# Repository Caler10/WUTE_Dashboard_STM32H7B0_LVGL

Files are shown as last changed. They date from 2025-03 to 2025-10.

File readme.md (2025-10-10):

# 针对WUTE车队电动方程式赛车开发的多功能仪表 WUTE_Dashboard

本人负责设计开发的WUTE第一代多功能自制仪表（该项目也是2023自创项目“针对电动方程式赛车开发的车身电子监控与人机交互系统”的人机交互部分），该仪表基于STM32H7B0VET6，采用5寸TFT高亮屏(800nit)，使用LVGL图形库绘制GUI界面并实时刷新赛车监测数据，具体功能如下：

功能说明：
1. 实时采集整车跑动数据，并在屏幕上实时刷新显示
2. 具备屏幕亮度随环境光自动调节功能
3. 集成跑马灯功能
4. 支持与整车CAN通讯
5. 集成2.4G无线数传模块（ESP8266模块）
6. 集成激活按钮、待驶按钮以及TSOFF、BMS、IMD指示灯

# 设计说明

## 硬件说明

硬件设计方面，采用立创EDA开发，四层板设计

PCB设计展示：

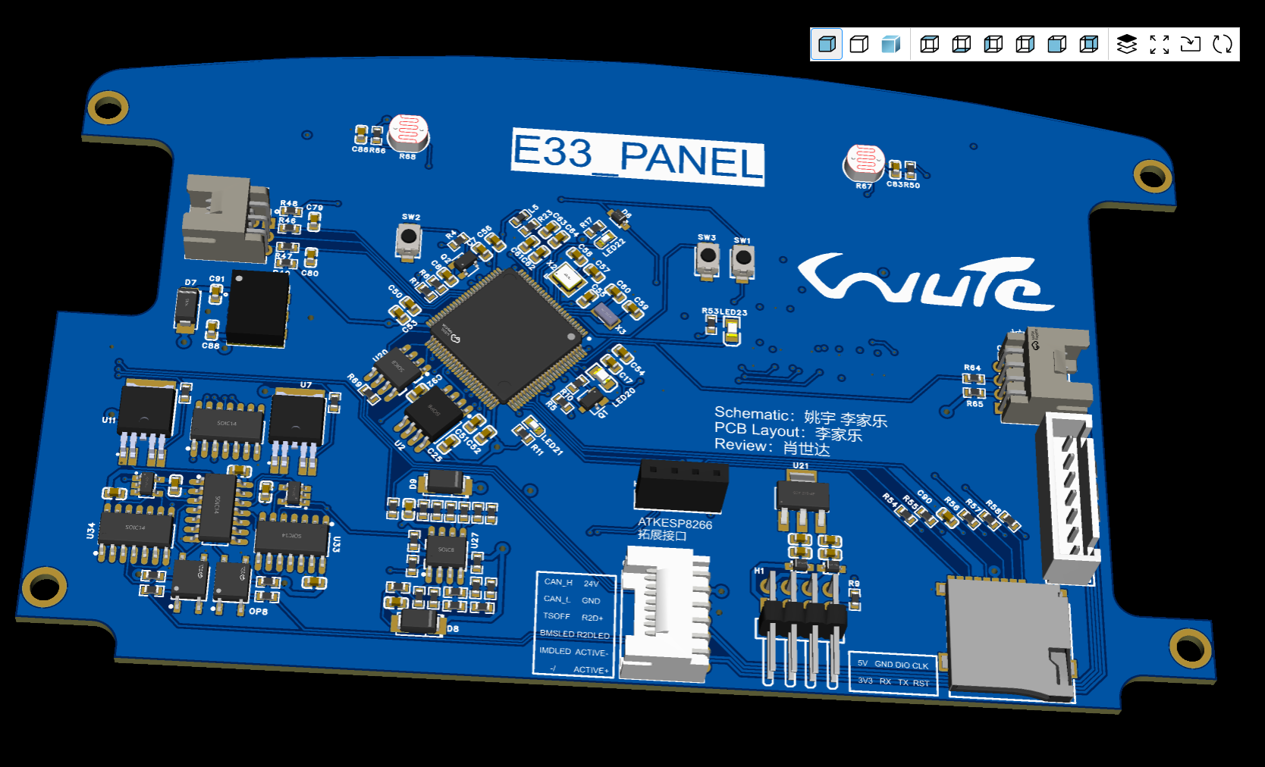
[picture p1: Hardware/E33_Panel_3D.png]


## 软件说明

开发平台：STM32H7B0VET6

开发环境：STM32cubeMX+Keil+VSCode

WUTE_Dashboard嵌入式软件分为Bootloader+App（为实现外部flash加载），App软件基于前后台的裸机系统开发，GUI采用LVGL图形库开发

App软件架构：基于CORE层+BSP层（+中间层LVGL）+APP层的架构开发

项目代码展示：

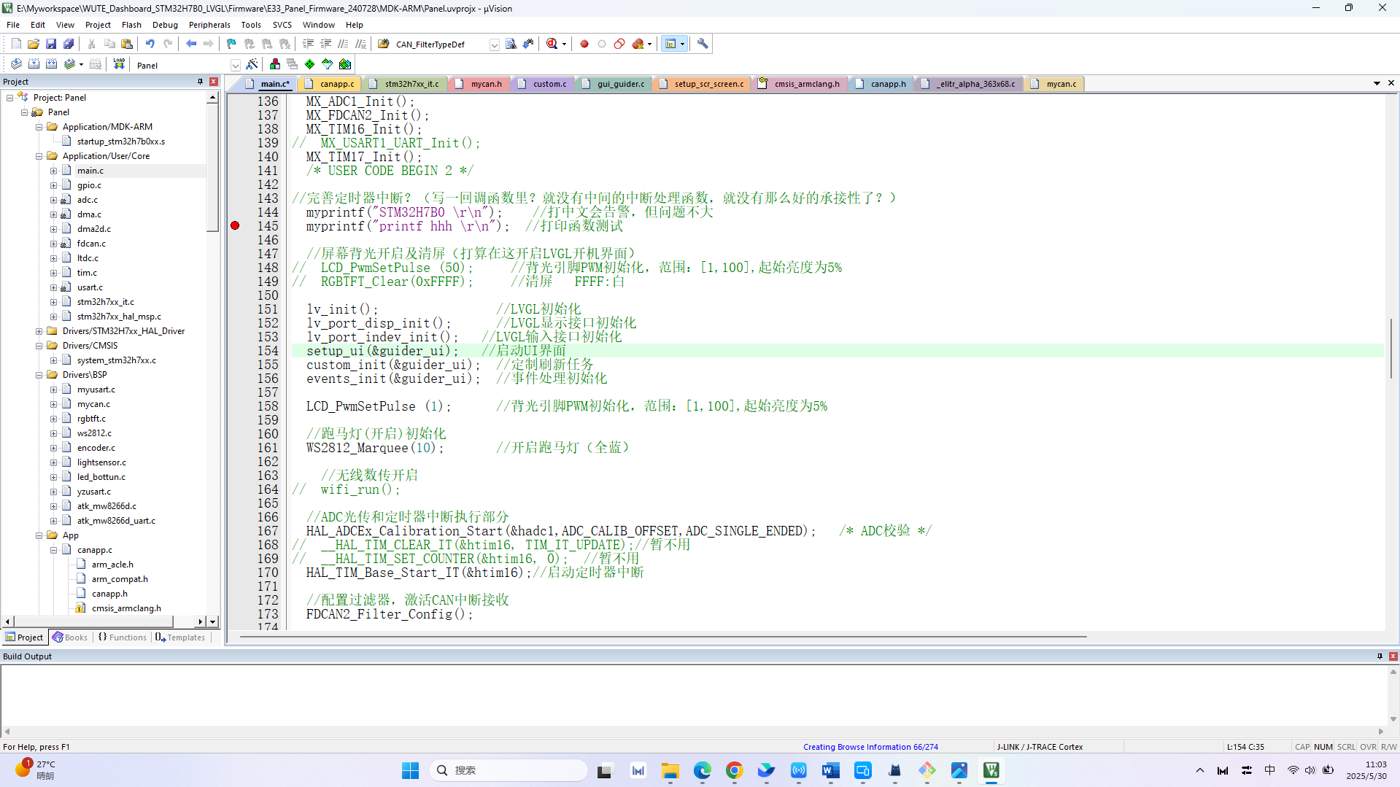
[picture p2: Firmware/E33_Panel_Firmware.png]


## 模型设计

仪表外壳分为前板和后板，仪表驱动板和屏幕封装在模型内部，通过沉头螺栓和热熔螺母进行固定，前后板之间采用密封胶填充间隙

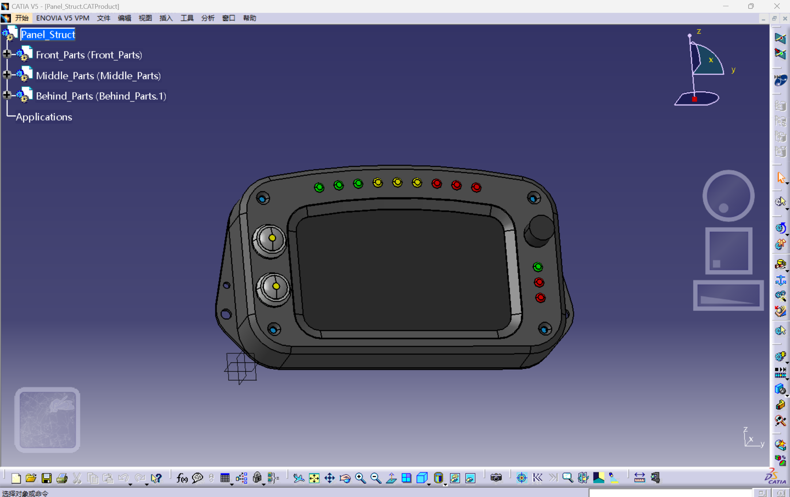
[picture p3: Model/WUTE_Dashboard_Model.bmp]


## GUI设计

仪表板界面UI采用单界面设计，在单界面整合了包括高压电池（电压、电流、温度、电量）、电机控制器（温度）、电机（转速、温度、功率）、各车身设备工作状态、DRS和TCS开启状态，以及制动油压、加速开度、转矩千分比等信息

GUI设计界面：

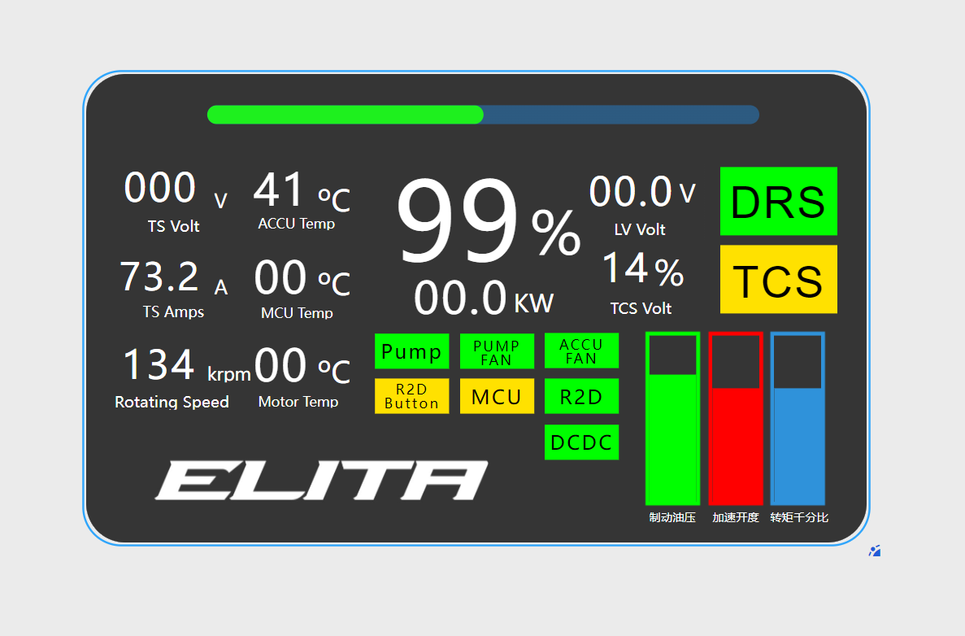
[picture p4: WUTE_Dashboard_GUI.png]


# 测试

屏幕静态显示测试，屏幕可正常显示设计的UI界面：

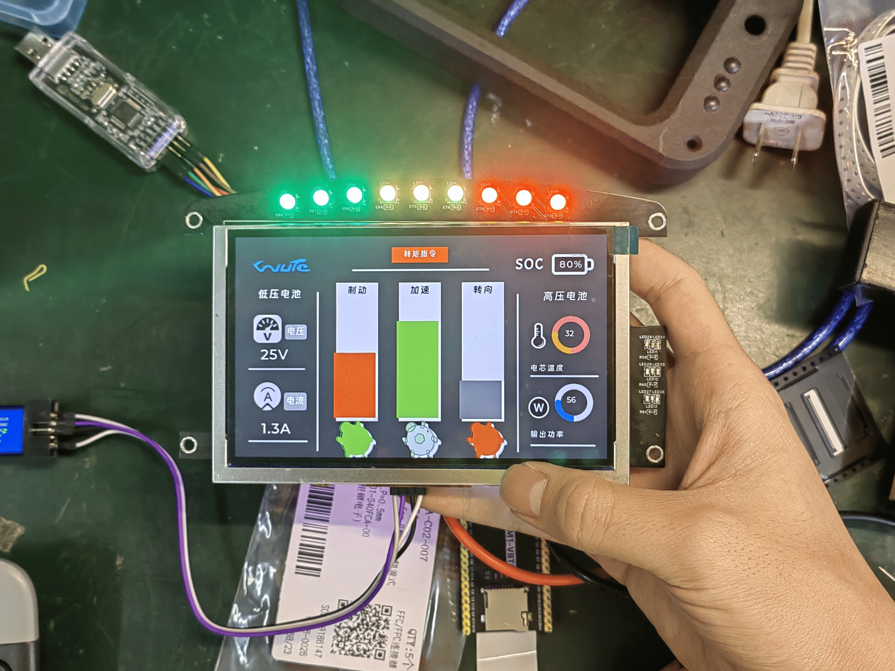
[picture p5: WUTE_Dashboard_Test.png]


屏幕动态刷新测试，仪表可正常解析CAN总线报文并将相关信息实时在屏幕和跑马灯上刷新：



# 项目成果

该仪表已顺利搭载在了WUTE车队2023赛季E33赛车和2024赛季E10赛车上并持续稳定运行，成为了赛车状况监测与可视化的重要途径，同时验证了其具备良好的抗振性与防水性

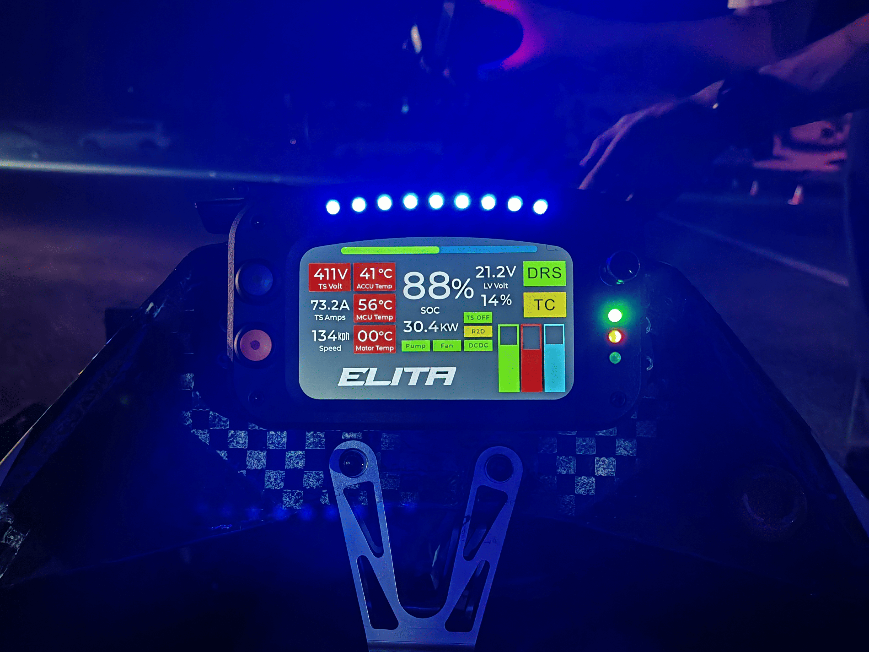
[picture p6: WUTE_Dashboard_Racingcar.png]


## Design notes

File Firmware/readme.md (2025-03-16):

# E33_Panel/WUTE_Dashboard裸机程序

开发平台：STM32H7B0VBT6
开发环境：MX+keil+VScode

---

# 软件架构

HAL库       
BSP         board support pack
APP         功能实现层
main函数    负责总调用执行

---

# 注意事项

无线透传的引脚未上位
慎用printf，加了相关的头文件，不报错但是会进半主机（导致不进main函数）然后无论烧录还是调试都执行不了程序找不到原因

开启了TIM7的定时器中断，现在主程序运行不了，中断程序也运行不了，除非把TIM中断关掉，就算在定时器中断不写任何东西，也还是这个问题
具体：运行不主动进主程序，进调试能使运行完主程序，然后进调试RESET后有报错Cannot access Memory (@ 0xe00ffff0, Read, Acc Size: 4 Byte)
2024.1.30回顾：是进半主机的问题

---

# 待完善问题

小心中断回调抢占导致低优先级的中断执行不了

跑马灯：
清屏＋跑马灯第一个灯灭不了

光传
已改，测试正常工作

串口打印
方案一：用自己的打印函数（只可打印），
方案二：使用MicroLIB来实现，哪种方案更好待考究
方案三：借鉴原子的透传打印函数（可打印可接收）

无线数传
wifi_run()；初始化正常，是ESP8266没有应答
原因：供电流不足

# 开发日志

## 20240411

最初可用版本

## 20240726

接入PDB、VCU报文
优化GUI显示
拓展PUMP、DRS、R2D按钮、MCU Ready、低压电池电压等数据的显示
调整跑马灯驱动（由随电池箱输出功率改为随电机转速变化），降低跑马灯亮度
解决DRS按钮按下DRS启动延时大的问题，仪表、VCU共用对PDB的指令报文
对照DBC校核显示数据（无误）

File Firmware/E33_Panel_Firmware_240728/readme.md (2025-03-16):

/**
 **********************************************************************************************************
 *项目名称：E33_Panel_裸机版程序
 *开发平台：STM32H7B0VBT6
 *开发环境：MX+keil+VScode
 **********************************************************************************************************
 */

/**********************************************************************************************************/
现况：
开启了TIM7的定时器中断，现在主程序运行不了，中断程序也运行不了，除非把TIM中断关掉，就算在定时器中断不写任何东西，也还是这个问题
具体：运行不主动进主程序，进调试能使运行完主程序，然后进调试RESET后有报错Cannot access Memory (@ 0xe00ffff0, Read, Acc Size: 4 Byte)
2024.1.30回顾：是进半主机的问题

/**********************************************************************************************************/

软件架构：
HAL库
BSP（board support pack）
APP
main总调用执行

/**********************************************************************************************************/

注意事项：
无线透传的引脚未上位
慎用printf，加了相关的头文件，不报错但是会进半主机（导致不进main函数）然后无论烧录还是调试都执行不了程序找不到原因

/**********************************************************************************************************/

待改进：小心中断回调抢占导致低优先级的中断执行不了

跑马灯：
清屏＋跑马灯第一个灯灭不了

光传
已改，测试正常工作

串口打印
方案一：用自己的打印函数（只可打印），
方案二：使用MicroLIB来实现，哪种方案更好待考究
方案三：借鉴原子的透传打印函数（可打印可接收）

无线数传
wifi_run()；初始化正常，是ESP8266没有应答
原因：供电流不足

20240726更新日志：
接入PDB、VCU报文
优化GUI显示
拓展PUMP、DRS、R2D按钮、MCU Ready、低压电池电压等数据的显示
调整跑马灯驱动（由随电池箱输出功率改为随电机转速变化），降低跑马灯亮度
解决DRS按钮按下DRS启动延时大的问题，仪表、VCU共用对PDB的指令报文
对照DBC校核显示数据（无误）

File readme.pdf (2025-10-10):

readme.md | 2025-10-10

# 针对WUTE车队电动方程式赛车开发的多功能仪表

# WUTE_Dashboard

本人负责设计开发的WUTE第一代自制仪表（该项目也是2023自创项目“针对电动方程式赛车开发的车身电子监 控与人机交互系统”的人机交互部分），一款基于STM32H7B0VET6，采用5寸TFT高亮屏(800nit)，使用LVGL图形 库绘制GUI界面并实时刷新赛车监测数据的多功能仪表，具体功能如下：

功能说明：

1. 集成跑马灯功能
2. 实时采集整车跑动数据，并在屏幕上实时刷新显示
3. 具备屏幕亮度随环境光自动调节功能
4. 支持与整车CAN通讯
5. 集成2.4G无线数传模块（ESP8266模块）
6. 集成激活按钮、待驶按钮以及TSOFF、BMS、IMD指示灯

# 设计说明

## 硬件说明

PCB设计展示：

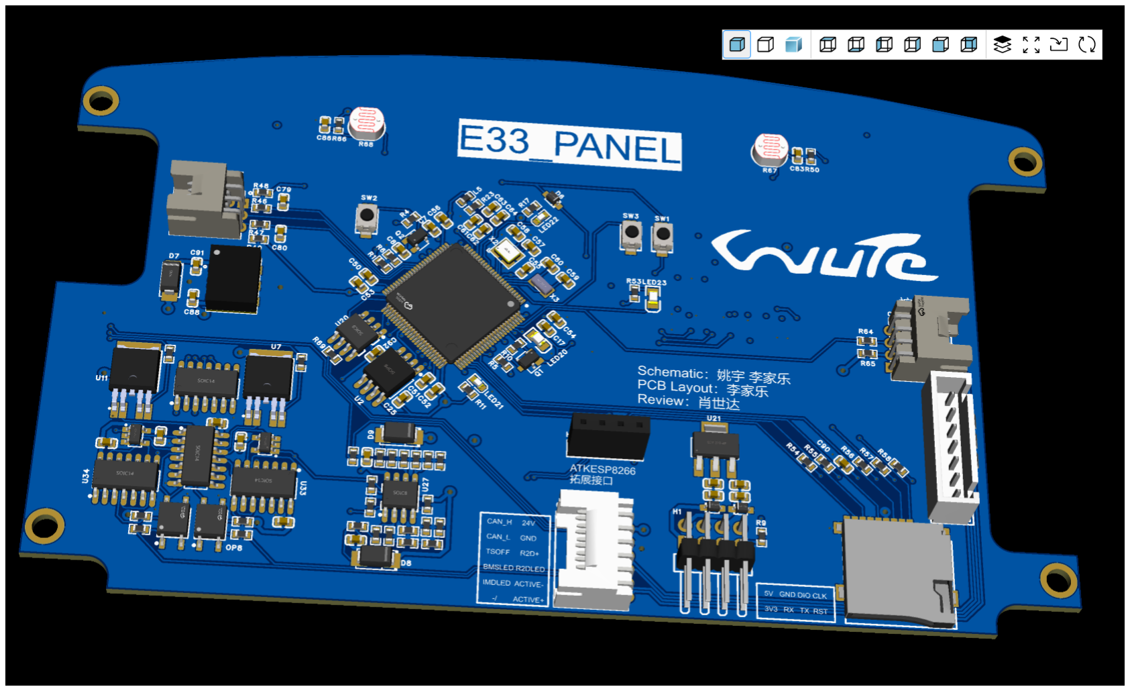
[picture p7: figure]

## 软件说明

WUTE_Dashboard嵌入式软件基于STM32cubeIDE+Keil开发，软件采用Bootloader+App的设计方案（为实现外 部flash加载），App软件基于前后台的裸机系统开发，GUI采用LVGL图形库开发

项目代码展示：


## 模型设计

仪表外壳分为前板和后板，仪表驱动板和屏幕封装在模型内部，通过沉头螺栓和热熔螺母进行固定，前后板之 间采用密封胶填充间隙


## GUI设计

仪表板界面UI采用单界面设计，在单界面整合了包括高压电池（电压、电流、温度、电量）、电机控制器（温 度）、电机（转速、温度、功率）、各车身设备工作状态、DRS和TCS开启状态，以及制动油压、加速开度、转 矩千分比等信息

GUI设计界面：

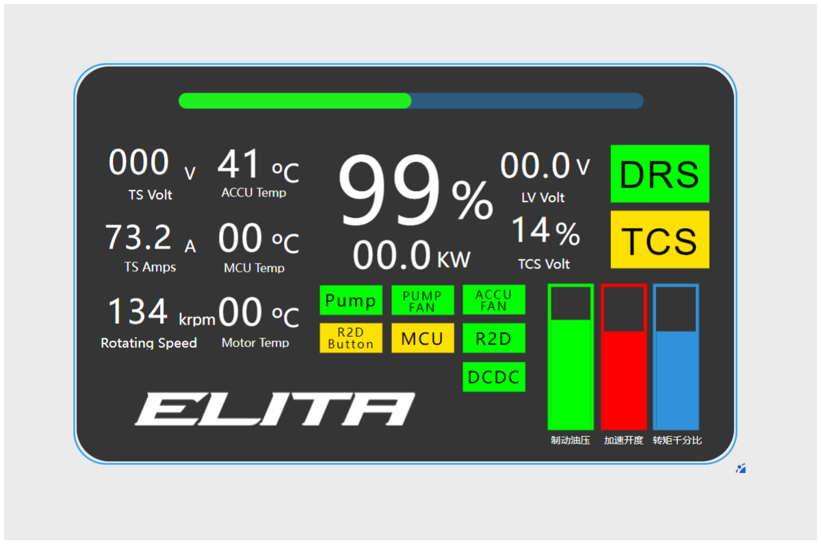
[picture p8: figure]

测试

屏幕静态显示测试，屏幕可正常显示设计的UI界面：

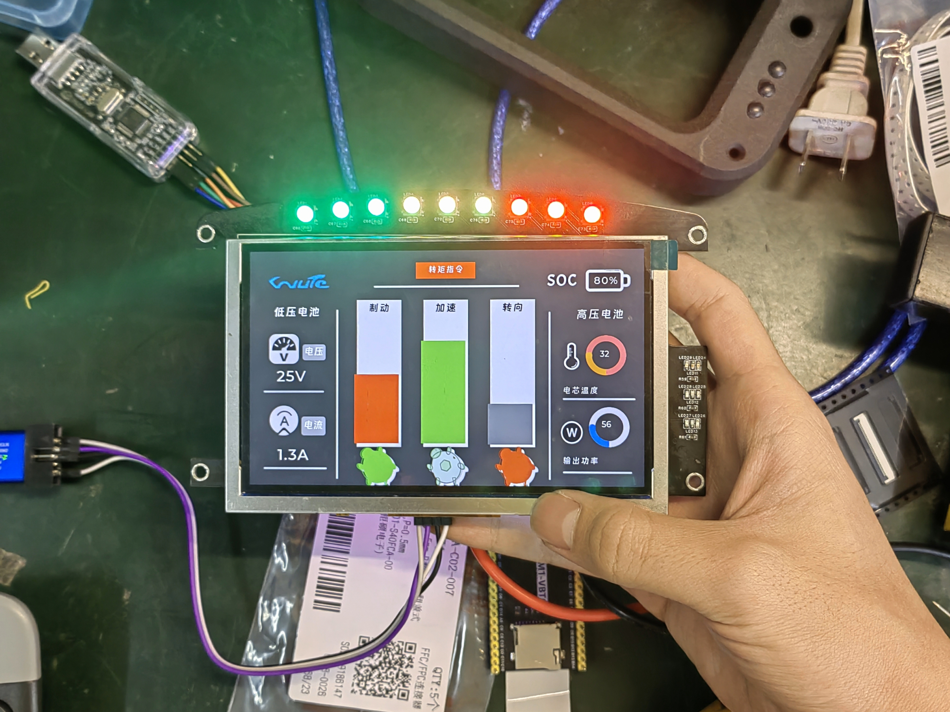
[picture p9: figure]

屏幕动态刷新测试，仪表可正常解析CAN总线报文并将相关信息实时在屏幕和跑马灯上刷新：

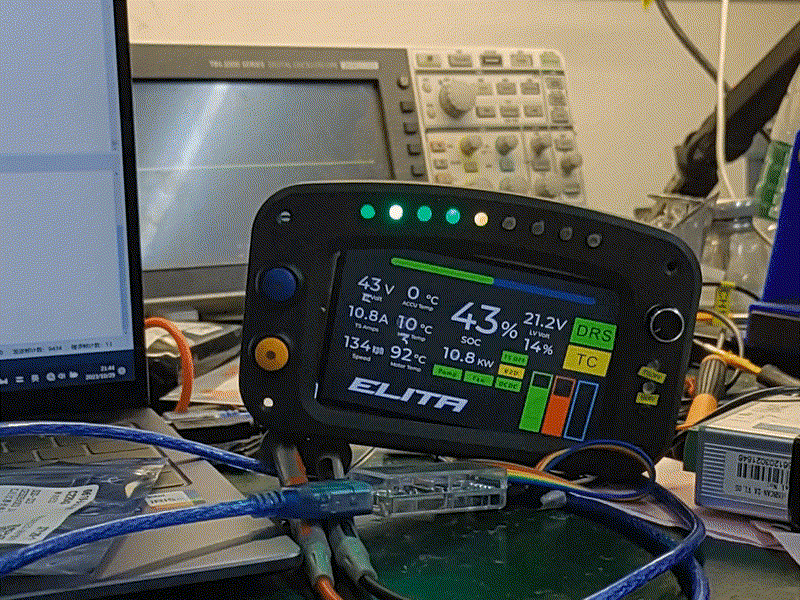
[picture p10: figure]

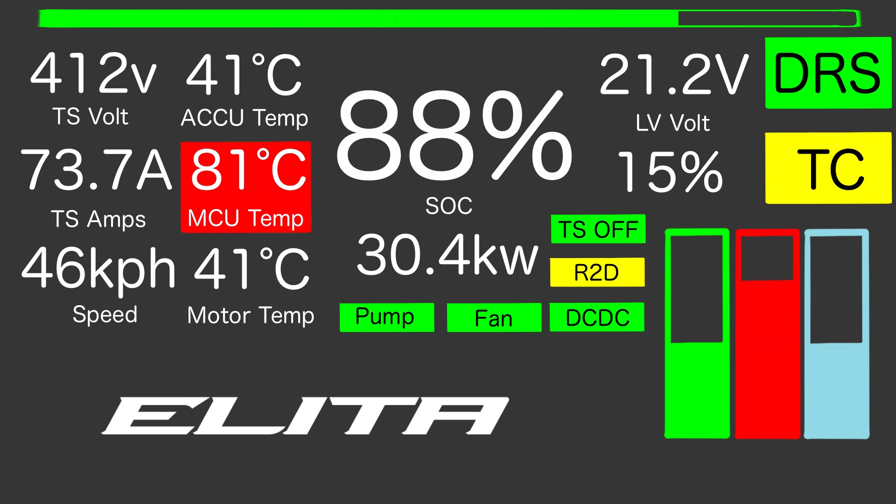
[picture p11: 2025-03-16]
Firmware/E33_Panel_Firmware_240728/GUI.jpg

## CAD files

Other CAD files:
Model/3D_PCB_20120916/3D_PCB1_2023-09-16.CATProduct
Model/3D_PCB_20120916/COMPOUND.CATPart
Model/3D_PCB_20120916/COMPOUND_1.CATPart
Model/3D_PCB_20120916/COMPOUND_10.CATPart
Model/3D_PCB_20120916/COMPOUND_11.CATPart
Model/3D_PCB_20120916/COMPOUND_12.CATPart
Model/3D_PCB_20120916/COMPOUND_13.CATPart
Model/3D_PCB_20120916/COMPOUND_14.CATPart
Model/3D_PCB_20120916/COMPOUND_15.CATPart
Model/3D_PCB_20120916/COMPOUND_16.CATPart
Model/3D_PCB_20120916/COMPOUND_17.CATPart
Model/3D_PCB_20120916/COMPOUND_18.CATPart
Model/3D_PCB_20120916/COMPOUND_19.CATPart
Model/3D_PCB_20120916/COMPOUND_2.CATPart
Model/3D_PCB_20120916/COMPOUND_3.CATPart
Model/3D_PCB_20120916/COMPOUND_4.CATPart
Model/3D_PCB_20120916/COMPOUND_5.CATPart
Model/3D_PCB_20120916/COMPOUND_6.CATPart
Model/3D_PCB_20120916/COMPOUND_7.CATPart
Model/3D_PCB_20120916/COMPOUND_8.CATPart
Model/3D_PCB_20120916/COMPOUND_9.CATPart
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

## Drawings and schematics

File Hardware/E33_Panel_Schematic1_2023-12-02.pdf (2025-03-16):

# RESET及BOOT电路

## 无误（R5电阻重选）

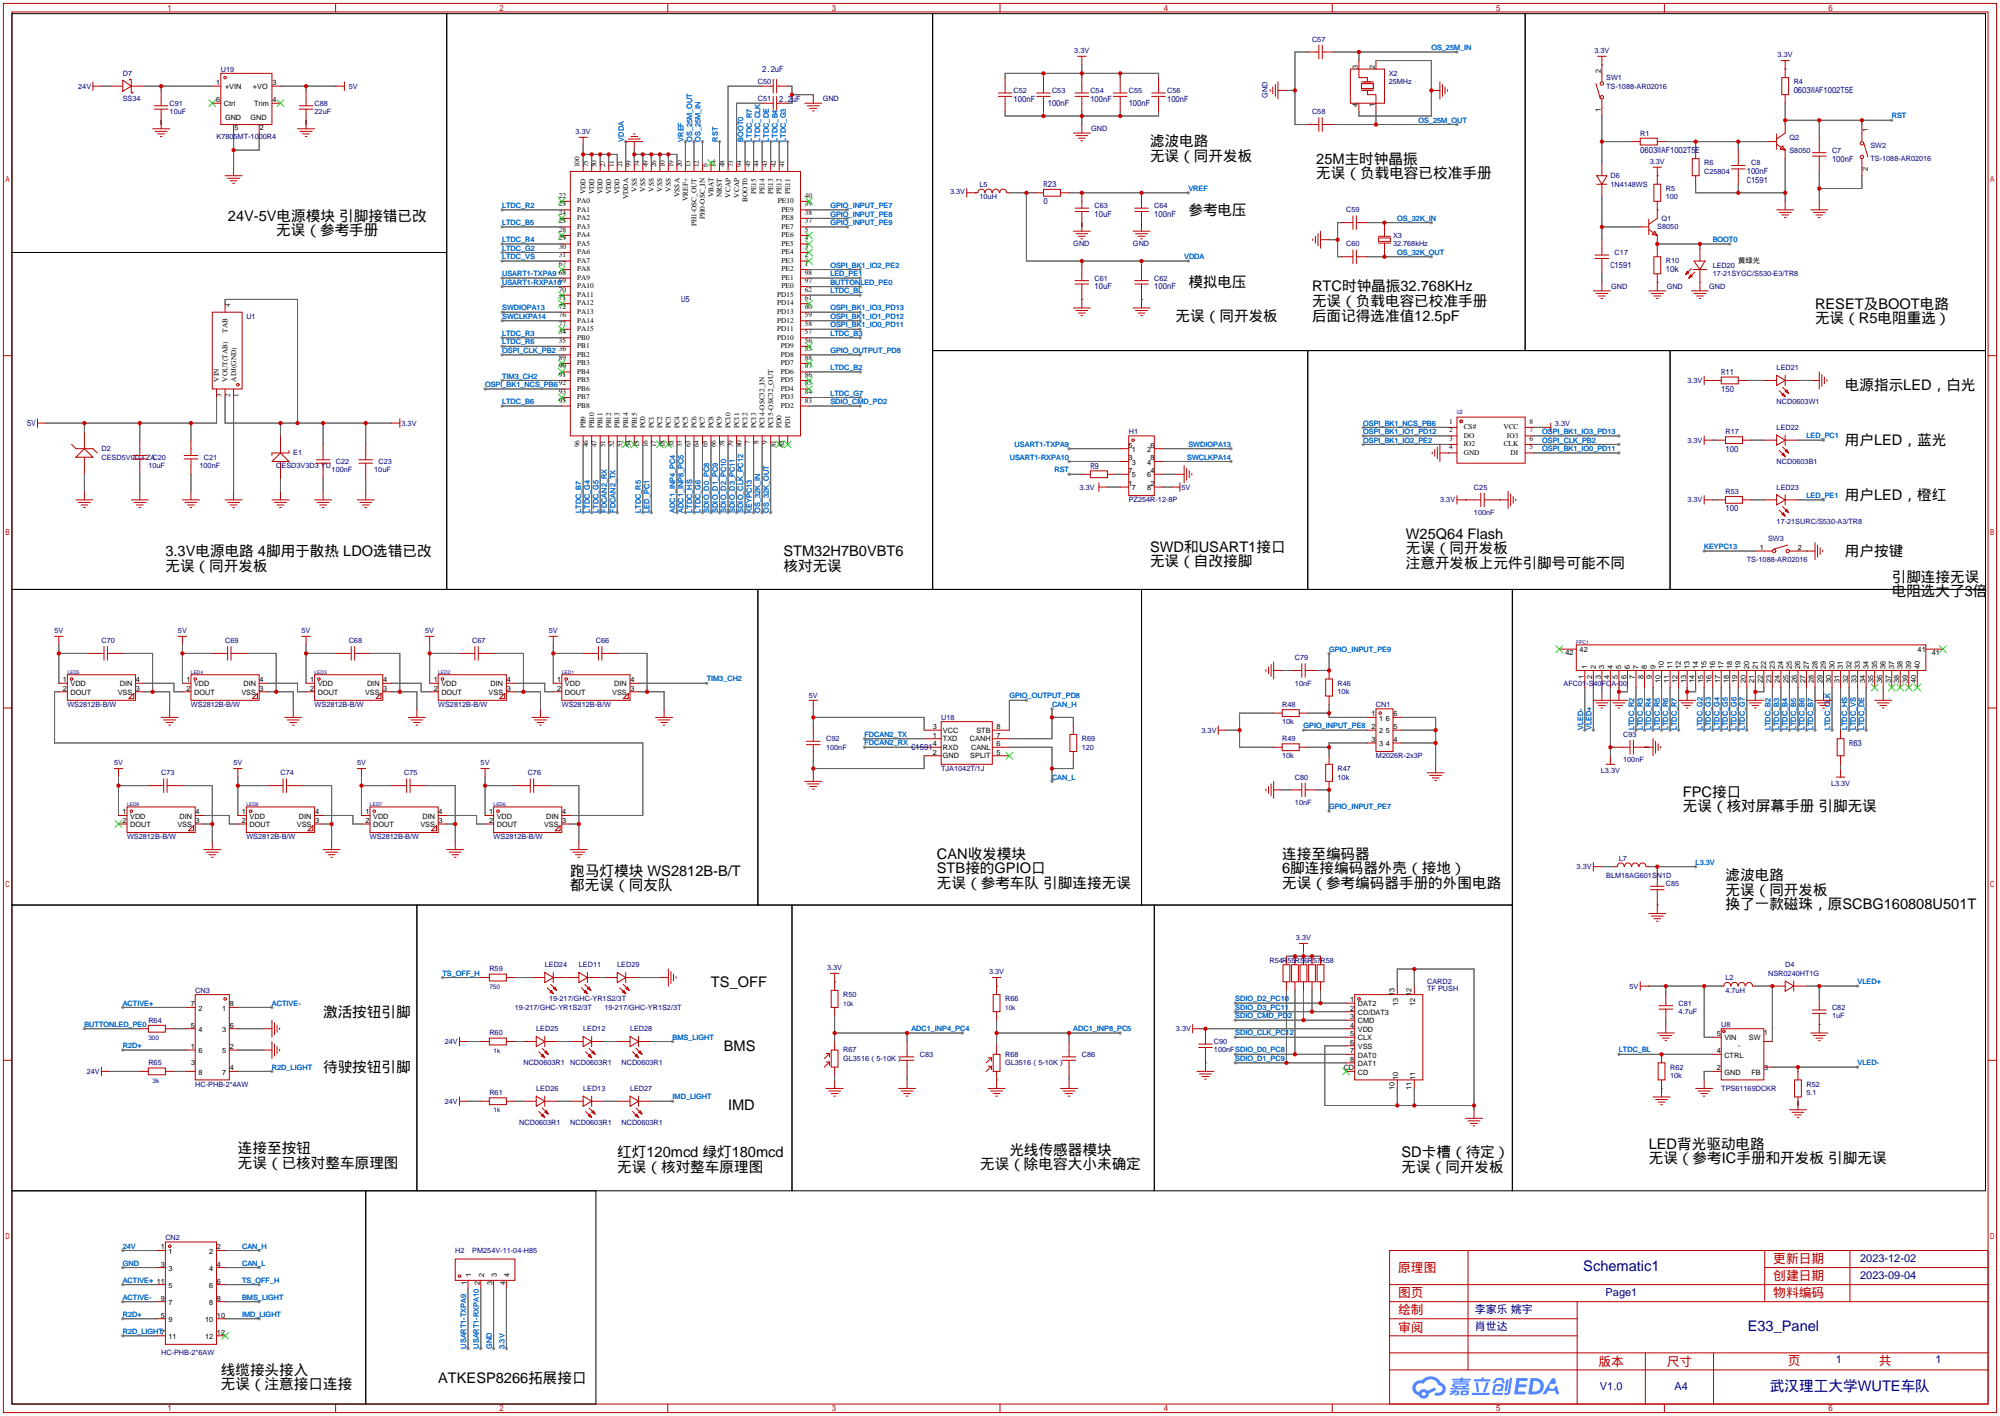
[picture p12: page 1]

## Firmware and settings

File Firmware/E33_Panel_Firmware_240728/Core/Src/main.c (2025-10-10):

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
/* Includes ------------------------------------------------------------------*/
#include "main.h"
#include "adc.h"
#include "dma.h"
#include "dma2d.h"
#include "fdcan.h"
#include "ltdc.h"
#include "tim.h"
#include "usart.h"
#include "gpio.h"

/* USER CODE BEGIN Includes */
#include "mycan.h"
#include "rgbtft.h"
#include "myusart.h"
#include "ws2812.h"
#include "custom.h"
#include "encoder.h"
#include "lightsensor.h"
#include "yzusart.h"
#include "atk_mw8266d.h"
#include "atk_mw8266d_uart.h"

#include "lvgl.h"
#include "lv_port_disp_template.h"
#include "lv_port_indev_template.h"
#include "gui_guider.h"
#include "events_init.h"

#include "wifiapp.h"//APP级别的

/* USER CODE END Includes */


/* USER CODE BEGIN PV */
lv_ui guider_ui;//guider_ui
/* USER CODE END PV */

void SystemClock_Config(void);
static void MPU_Config(void);
/**
  * @brief  The application entry point.
  * @retval int
  */
int main(void)
{
  /* USER CODE BEGIN 1 */
	
//CAN变量
//	uint8_t i = 0;
//	uint8_t canbuf[8]={0};
//	uint8_t res;//指示是否成功
//	uint8_t rxlen = 0;

	uint8_t res;
  /* USER CODE END 1 */

  /* MPU Configuration--------------------------------------------------------*/
  MPU_Config();
/* Enable the CPU Cache */

  /* Enable I-Cache---------------------------------------------------------*/
  SCB_EnableICache();

  /* Enable D-Cache---------------------------------------------------------*/
  SCB_EnableDCache();

  /* MCU Configuration--------------------------------------------------------*/

  /* Reset of all peripherals, Initializes the Flash interface and the Systick. */
  HAL_Init();

  /* Configure the system clock */
  SystemClock_Config();

  /* Initialize all configured peripherals */
  MX_GPIO_Init();
  MX_DMA_Init();
  MX_TIM4_Init();
  MX_LTDC_Init();
  MX_TIM3_Init();
  MX_DMA2D_Init();
  MX_ADC1_Init();
  MX_FDCAN2_Init();
  MX_TIM16_Init();
//  MX_USART1_UART_Init();
  MX_TIM17_Init();
  /* USER CODE BEGIN 2 */

//完善定时器中断？（写一回调函数里？就没有中间的中断处理函数，就没有那么好的承接性了？）
	myprintf("STM32H7B0 \r\n");    //打中文会告警，但问题不大
	myprintf("printf hhh \r\n");	//打印函数测试

	//屏幕背光开启及清屏（打算在这开启LVGL开机界面）
//  LCD_PwmSetPulse (50);			//背光引脚PWM初始化，范围：[1,100],起始亮度为5%
//  RGBTFT_Clear(0xFFFF);		  //清屏   FFFF:白

	lv_init();					     	//LVGL初始化
	lv_port_disp_init();		 	//LVGL显示接口初始化
	lv_port_indev_init();		//LVGL输入接口初始化
	setup_ui(&guider_ui);		//启动UI界面
	custom_init(&guider_ui);	//定制刷新任务
	events_init(&guider_ui);	//事件处理初始化
	
	LCD_PwmSetPulse (1);			//背光引脚PWM初始化，范围：[1,100],起始亮度为5%
	
	//跑马灯(开启)初始化
	WS2812_Marquee(10);  			//开启跑马灯（全蓝）
	
		//无线数传开启
//	wifi_run(); 
	
	//ADC光传和定时器中断执行部分
	HAL_ADCEx_Calibration_Start(&hadc1,ADC_CALIB_OFFSET,ADC_SINGLE_ENDED);   /* ADC校验 */
//	__HAL_TIM_CLEAR_IT(&htim16, TIM_IT_UPDATE);//暂不用
//	__HAL_TIM_SET_COUNTER(&htim16, 0);	//暂不用
	HAL_TIM_Base_Start_IT(&htim16);//启动定时器中断
	
	//配置过滤器，激活CAN中断接收
	FDCAN2_Filter_Config();
	
	HAL_Delay(2000);
	WS2812_Marquee(0);//标志初始化阶段结束
	
//	wifiprintf("panel init finish");
//	Fdcan_Send_Msg(TxData, FDCAN_DLC_BYTES_1);
  /* USER CODE END 2 */

  /* Infinite loop */
  /* USER CODE BEGIN WHILE */
  while (1)
  {
    /* USER CODE END WHILE */

    /* USER CODE BEGIN 3 */
	
		//LVGL实时任务处理
		lv_task_handler();	// LVGL进程 redraw the screen if required, handle input devices, animation etc.
//		HAL_Delay(1000);
				
//		HAL_GPIO_TogglePin (GPIOC,  GPIO_PIN_1);//指示灯闪烁 最后程序建议把内部指示灯都关掉，防止影响光传工作
		HAL_Delay(5);
  }
  /* USER CODE END 3 */
}

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
/* MPU Configuration */

void MPU_Config(void)
{
  MPU_Region_InitTypeDef MPU_InitStruct = {0};

  /* Disables the MPU */
  HAL_MPU_Disable();

  /** Initializes and configures the Region and the memory to be protected
  */
  MPU_InitStruct.Enable = MPU_REGION_ENABLE;
  MPU_InitStruct.Number = MPU_REGION_NUMBER0;
  MPU_InitStruct.BaseAddress = 0x24000000;
  MPU_InitStruct.Size = MPU_REGION_SIZE_1MB;
  MPU_InitStruct.SubRegionDisable = 0;
  MPU_InitStruct.TypeExtField = MPU_TEX_LEVEL0;
  MPU_InitStruct.AccessPermission = MPU_REGION_FULL_ACCESS;
  MPU_InitStruct.DisableExec = MPU_INSTRUCTION_ACCESS_ENABLE;
  MPU_InitStruct.IsShareable = MPU_ACCESS_NOT_SHAREABLE;
  MPU_InitStruct.IsCacheable = MPU_ACCESS_NOT_CACHEABLE;
  MPU_InitStruct.IsBufferable = MPU_ACCESS_NOT_BUFFERABLE;

  HAL_MPU_ConfigRegion(&MPU_InitStruct);
  /* Enables the MPU */
  HAL_MPU_Enable(MPU_PRIVILEGED_DEFAULT);

}

/**
  * @brief  This function is executed in case of error occurrence.
  * @retval None
  */
void Error_Handler(void)
{
  /* USER CODE BEGIN Error_Handler_Debug */
  /* User can add his own implementation to report the HAL error return state */
  __disable_irq();
  while (1)
  {
  }
  /* USER CODE END Error_Handler_Debug */
}

#ifdef  USE_FULL_ASSERT
/**
  * @brief  Reports the name of the source file and the source line number
  *         where the assert_param error has occurred.
  * @param  file: pointer to the source file name
  * @param  line: assert_param error line source number
  * @retval None
  */
void assert_failed(uint8_t *file, uint32_t line)
{
  /* USER CODE BEGIN 6 */
  /* User can add his own implementation to report the file name and line number,
     ex: printf("Wrong parameters value: file %s on line %d\r\n", file, line) */
  /* USER CODE END 6 */
}
#endif /* USE_FULL_ASSERT */

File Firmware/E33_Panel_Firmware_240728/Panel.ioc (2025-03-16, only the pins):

Mcu.UserName=STM32H7B0VBTx
PA10.Signal=USART1_RX
PA13.Signal=DEBUG_JTMS-SWDIO
PA14.Signal=DEBUG_JTCK-SWCLK
PA3.Signal=LTDC_B5
PA5.Signal=LTDC_R4
PA6.Signal=LTDC_G2
PA7.Signal=LTDC_VSYNC
PA9.Signal=USART1_TX
PB0.Signal=LTDC_R3
PB1.Signal=LTDC_R6
PB10.Signal=LTDC_G4
PB11.Signal=LTDC_G5
PB12.Signal=FDCAN2_RX
PB13.Signal=FDCAN2_TX
PB15.Signal=GPIO_Output
PB5.Signal=S_TIM3_CH2
PB8.Signal=LTDC_B6
PB9.Signal=LTDC_B7
PC0.Signal=LTDC_R5
PC1.Signal=GPIO_Output
PC13.Signal=GPIO_Input
PC4.Signal=ADCx_INP4
PC6.Signal=LTDC_HSYNC
PC7.Signal=LTDC_G6
PD10.Signal=LTDC_B3
PD15.Signal=S_TIM4_CH4
PD3.Signal=LTDC_G7
PD8.Signal=GPIO_Output
PE1.Signal=GPIO_Output
PE11.Signal=LTDC_G3
PE12.Signal=LTDC_B4
PE13.Signal=LTDC_DE
PE14.Signal=LTDC_CLK
PE15.Signal=LTDC_R7
PE7.Signal=GPIO_Output
PE8.Signal=GPIO_Input
PE9.Signal=GPIO_Output
PH0-OSC_IN.Signal=RCC_OSC_IN
PH1-OSC_OUT.Signal=RCC_OSC_OUT

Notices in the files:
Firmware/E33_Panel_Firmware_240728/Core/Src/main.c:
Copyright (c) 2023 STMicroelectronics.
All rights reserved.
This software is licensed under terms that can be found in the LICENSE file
